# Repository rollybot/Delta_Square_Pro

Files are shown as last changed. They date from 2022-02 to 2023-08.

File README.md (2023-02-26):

# Delta Square Pro
Enclosed chamber-type Delta 3D printer.
You can find the BOM and some parts for this printer at www.rollybot.com website.

제품_Delta Square v1_대표이미지01
The current revision is V1.0.

## Highlights
- Delta (Enclosed chamber-type)
- Minimal design
- 180x180 build volume (bed size : 200mm)
- Enclosed chamber
- Integrated nozzle headset
- 220v / 110v AC
 
## Release History
### V1.0 Initial release (2022 February)
See https://

rollybot.com Logo

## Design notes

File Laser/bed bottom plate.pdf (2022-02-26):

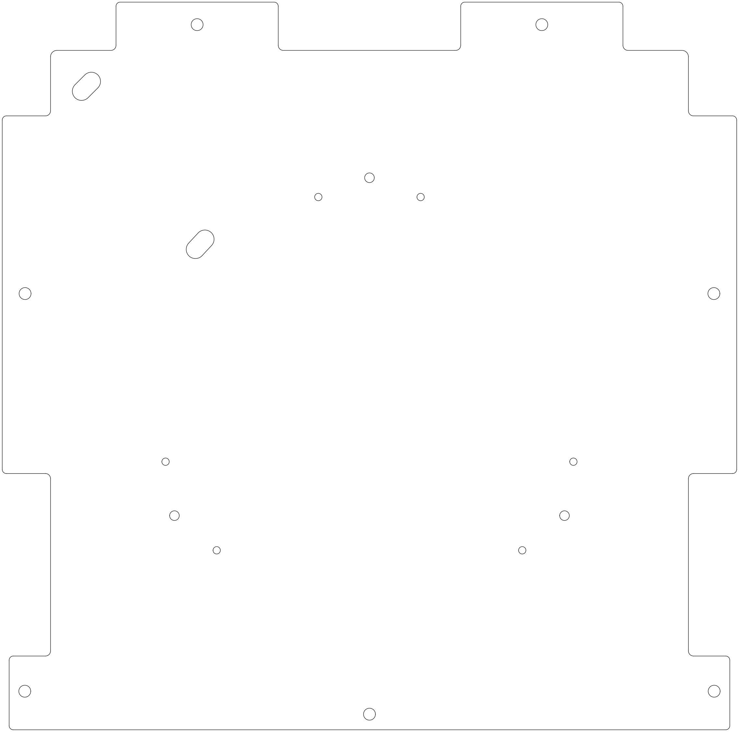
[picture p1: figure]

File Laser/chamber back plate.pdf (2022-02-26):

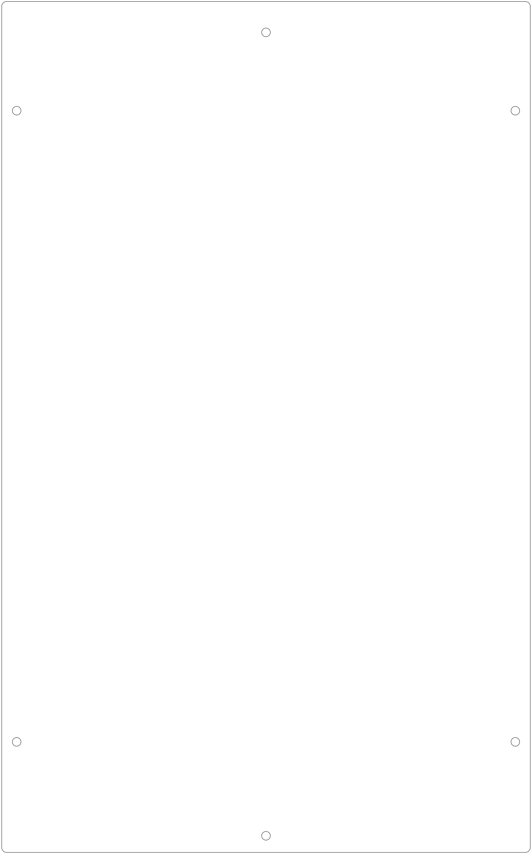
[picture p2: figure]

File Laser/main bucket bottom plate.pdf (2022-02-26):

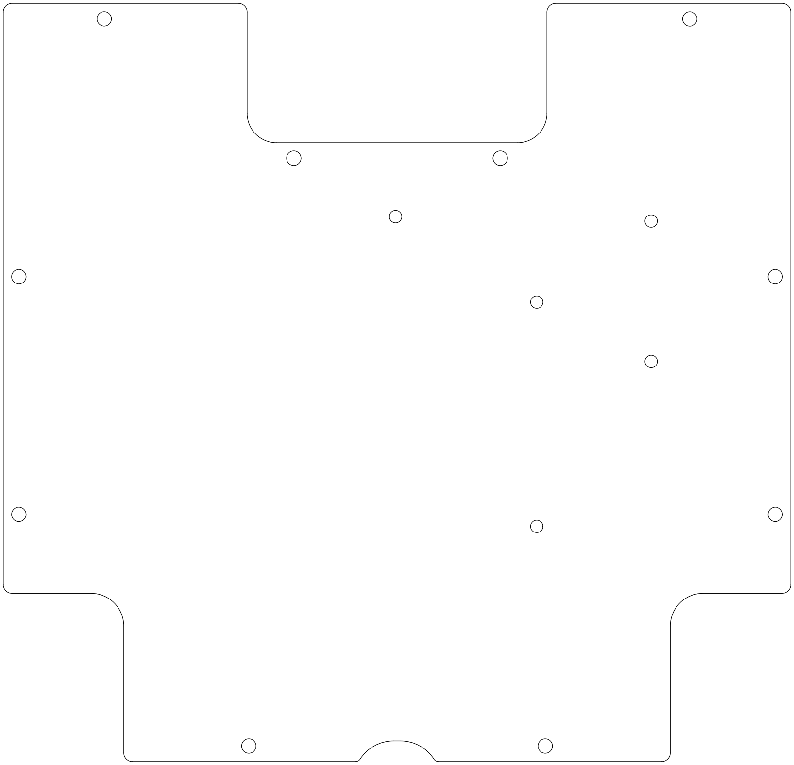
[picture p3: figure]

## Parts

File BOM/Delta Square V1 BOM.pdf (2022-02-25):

Model: Delta Square V1
Developer: rollybot.com
Component | details | Qty | Link
AL profile 2020 280mm | china standard | 6
AL profile 2020 320mm | china standard | 4
AL profile 2020 570mm | china standard | 5
2020 Corner Angle L Bracket | black | 28
20 Series T-nut | M5
GT2 Idler Timing Pulley | 20teeth,6width,5bore,no teeth
Knurled Brass Hot Melt Inset | M3, 5dia, 4.2length
Copper hollow rivet | M4, 4length
POM Bearings Pulley Wheel | 5bore, 21.5dia, 7depth
Right Angle USB Type B male to USB B female extension cable | 30cm
M3 Fisheye Effector Connector | 40mm, Aluminum
Lattice Glass Bed | 200mm, round
Fisheye Ball Bearing Rod Ends Joint | male thread M3
Hollow Carbon Rod | ID3 OD5, 200mm
SAMS socket head cap screw M5 | 10mm, silver
Self-locking nut M5
Hexagon socket button head cap screw M5 | 25mm, silver | 9
Hexagon socket button head cap screw M5 | 20mm, silver | 3
Hexagon socket button head cap screw M5 | 15mm, black
Hexagon socket button head cap screw M5 | 10mm, black
Hexagon socket button head cap screw M5 | 8mm, black
SAMS socket head cap screw M3 | 20mm, silver | 12
Self-locking nut M3
Hexagon socket button head cap screw M3 | 6mm, black

Bill of Materials

Hexagon socket button head cap screw M3 | 8mm, black
Hexagon socket button head cap screw M3 | 10mm, black
Hexagon socket button head cap screw M3 | 12mm, black
Hexagon socket button head cap screw M3 | 15mm, black
Hexagon socket button head cap screw M3 | 22mm, black | 2
Hexagon socket button head cap screw M3 | 35mm, black | 7
NEMA17 | 38mm or 40mm | 4
GT2 Timing Belt | 6mm width
GT2 Timing Pulley | 20teeth,6width,5bore | 3
GT2 Idler Pulley | 20teeth,6width,5bore,no teeth | 3
Print Head PCB | 1.6t | 1 | rollybot.com
Slider PCB | 1.6t | 3 | rollybot.com
Ramps1.4 | | 1
Arduino MEGA 2560 | | 1
2004 LCD | | 1
Timing belt | GT2, 6mm width
Timing belt torsion spring | 6mm width | 3
E3D v6 set (0.4mm nozzle) | | 1
FAN 30x30 | 12v, 10mm width | 2
FAN 50x50 | 12v, 10mm width | 1
CR10 extruder set | right hand type | 1
TMC2208 driver | standalone type | 4
Direct LAN cable | 24awg, 1M | 1
Spacer POM M5 | 12mm, ID5 OD9 | 9
PTFE tube | ID2 OD4
24AWG 2-wire cable
240V power cable
White heat shrink tube | OD 7mm

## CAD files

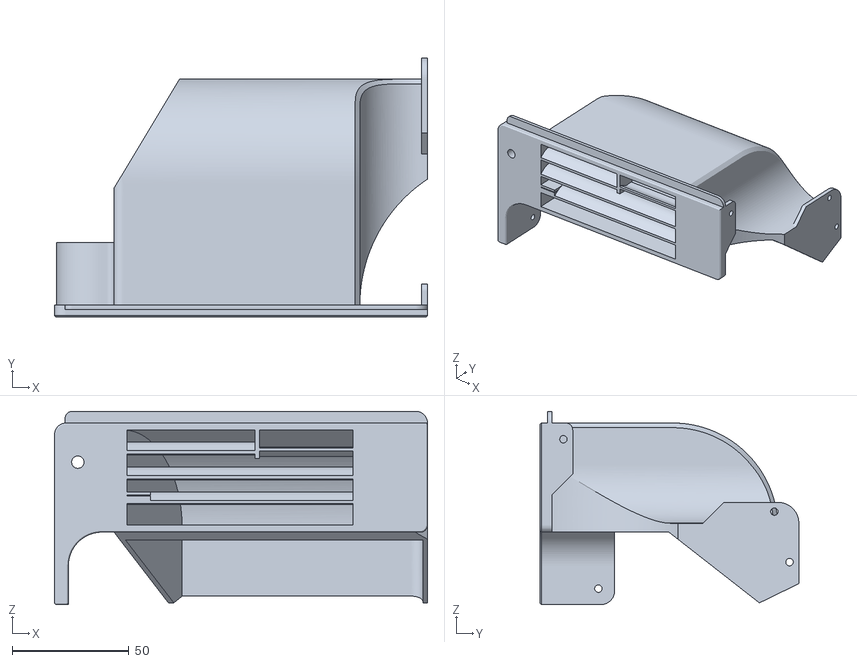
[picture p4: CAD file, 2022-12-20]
STLs/Filter mainvent_right.stl
160.0 x 111.0 x 82.9

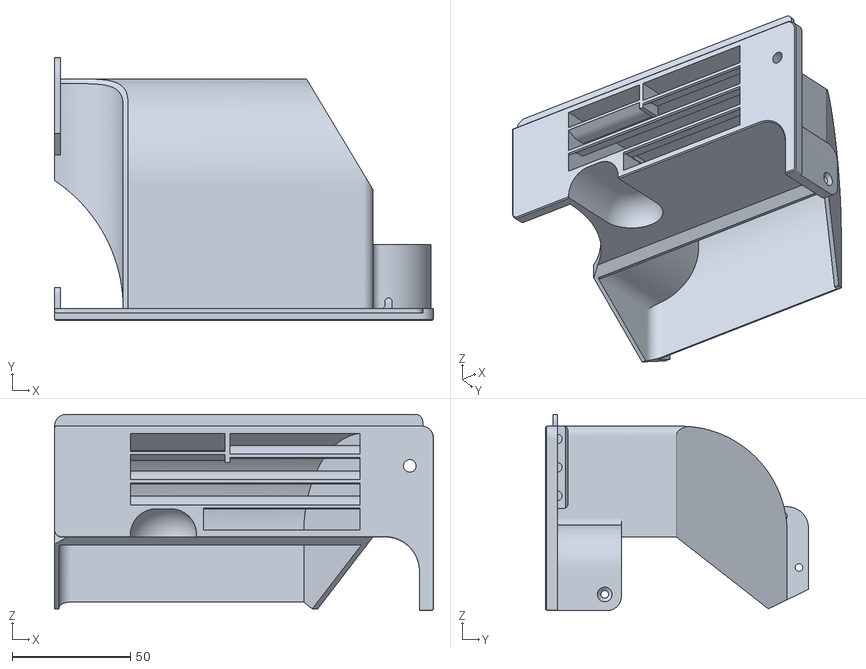
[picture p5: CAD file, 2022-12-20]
STLs/Filter mainvent_left.stl
160.0 x 111.0 x 82.9

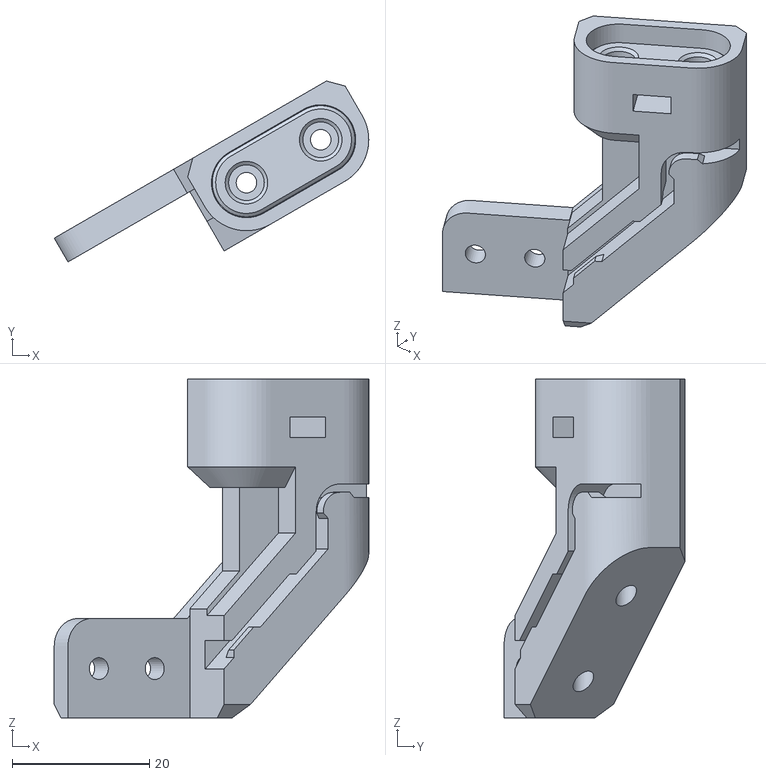
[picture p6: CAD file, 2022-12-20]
STLs/Acc/Fixed leveling sensor.stl
45.8 x 26.4 x 49.4

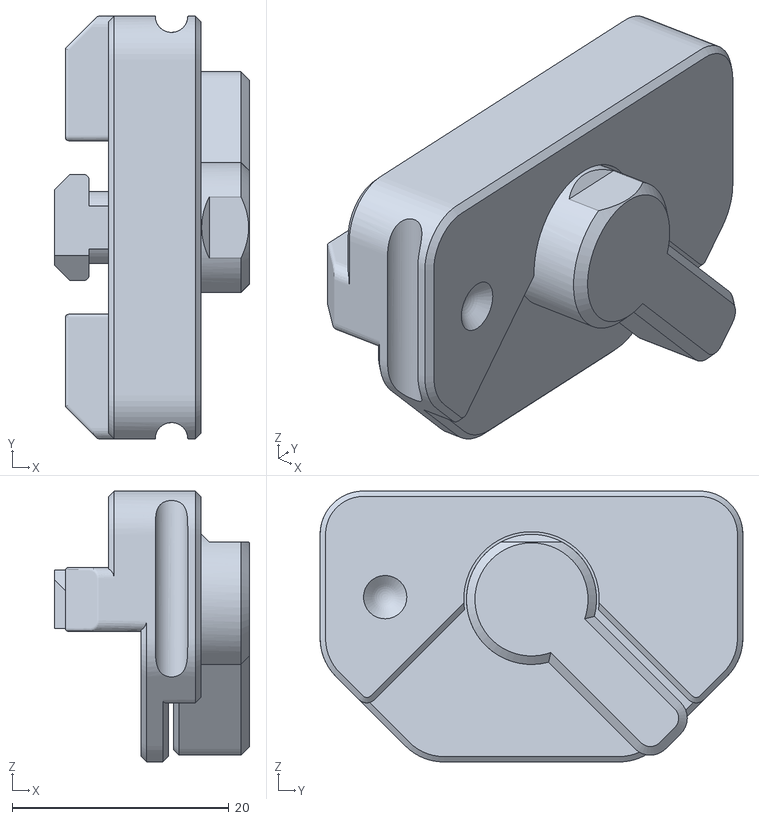
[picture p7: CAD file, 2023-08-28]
STLs/Panel_locker.stl
18.0 x 39.0 x 25.0

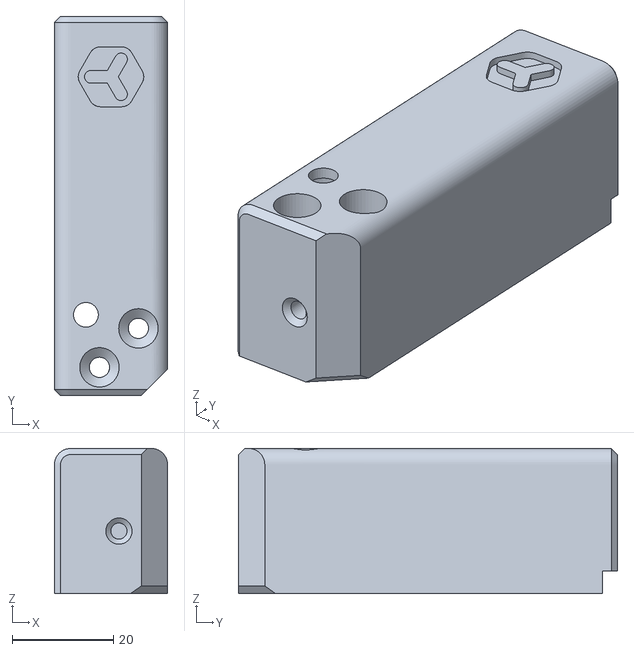
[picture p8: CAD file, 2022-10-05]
STLs/Acc/Filament 45cutter_body.stl
22.4 x 75.0 x 28.7

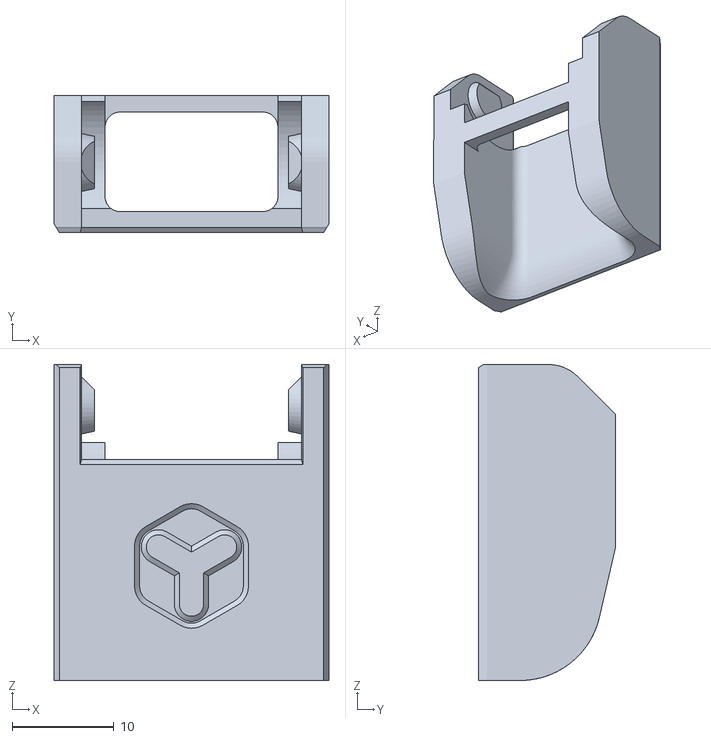
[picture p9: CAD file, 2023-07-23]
STLs/Wire_guide_33.stl
27.0 x 13.5 x 31.1

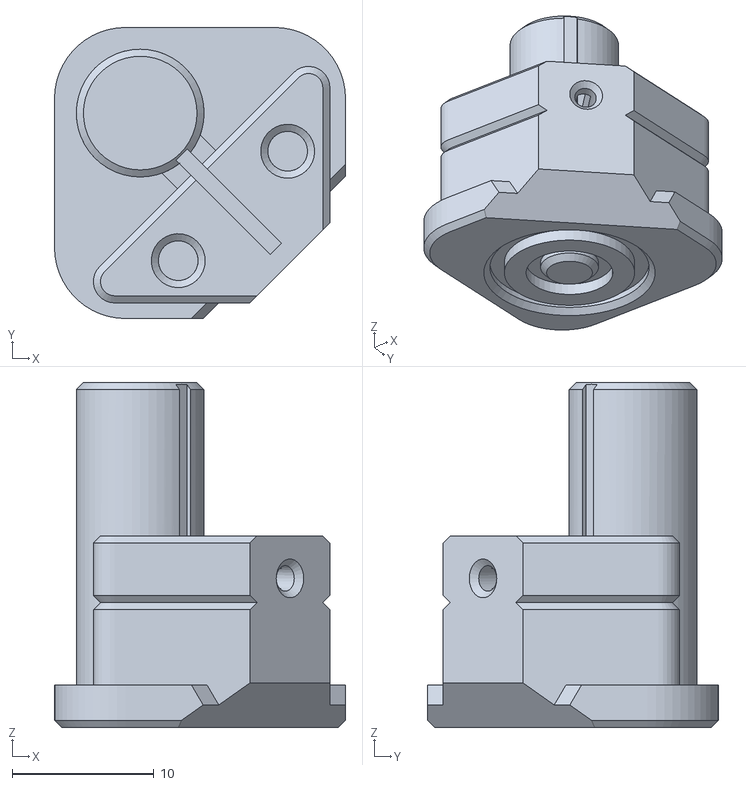
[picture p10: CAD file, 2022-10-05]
STLs/Acc/Filament 45cutter_pusher.stl
20.5 x 20.5 x 24.3

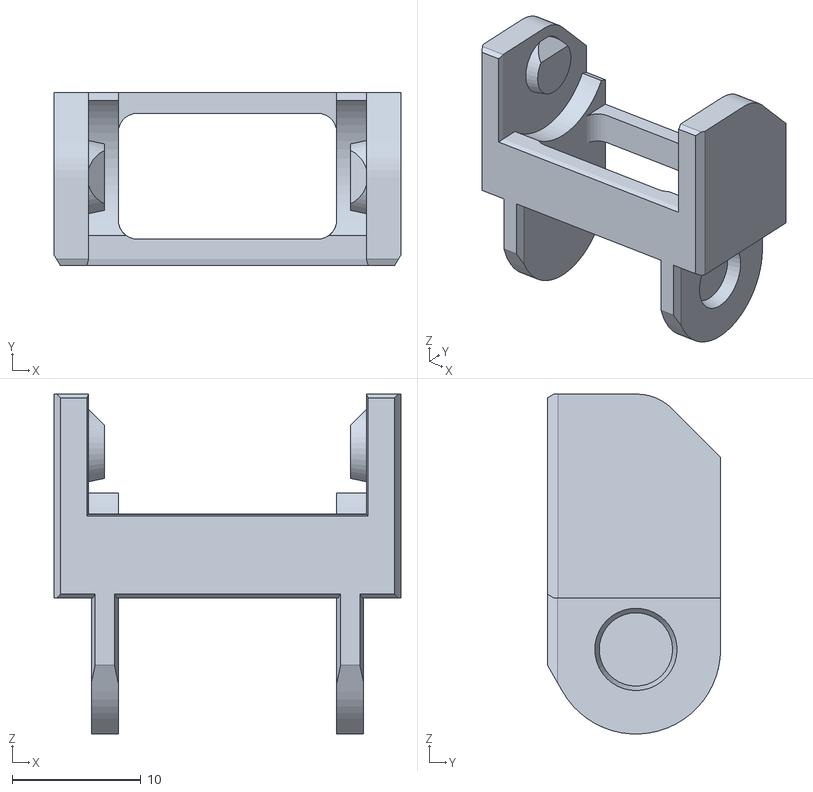
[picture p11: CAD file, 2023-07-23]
STLs/Wire_guide_23.stl
27.0 x 13.5 x 26.5

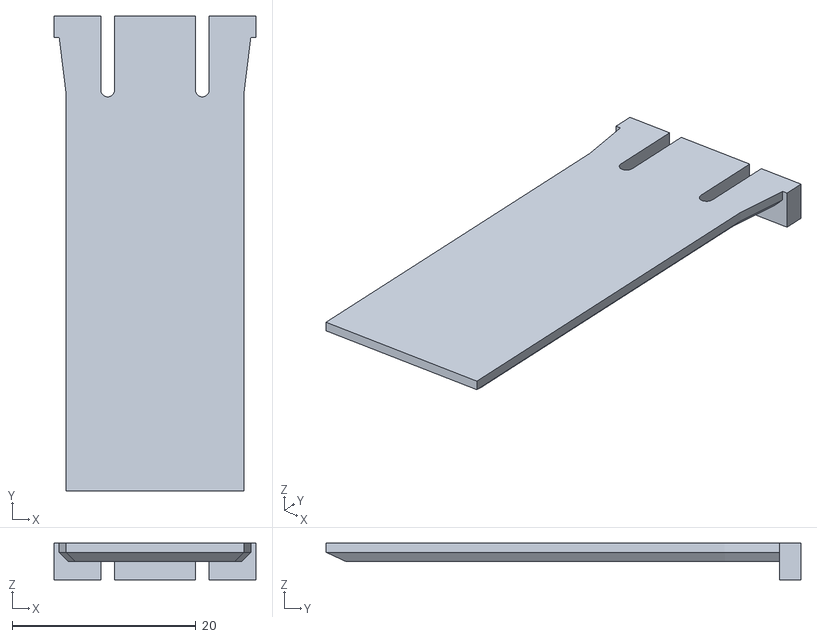
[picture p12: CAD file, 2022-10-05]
STLs/Acc/Filament 45cutter_cover.stl
22.0 x 51.7 x 4.00

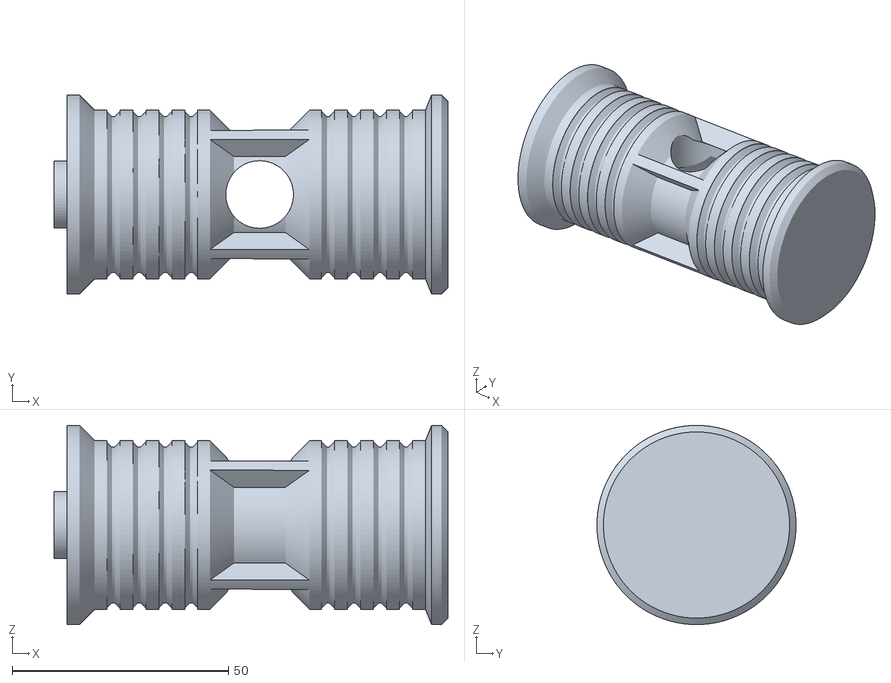
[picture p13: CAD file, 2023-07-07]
STLs/spool core.stl
91.0 x 46.0 x 46.0

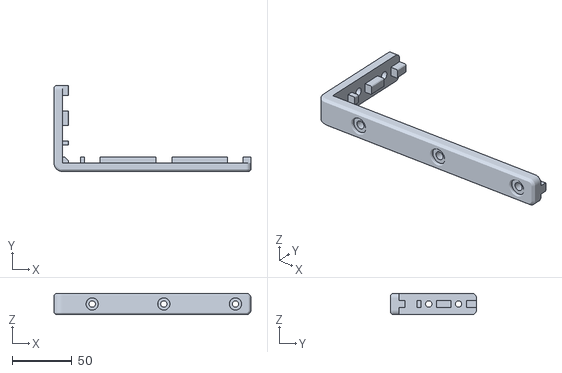
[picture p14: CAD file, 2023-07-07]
STLs/Frame longLbar.stl
165.0 x 72.0 x 18.0

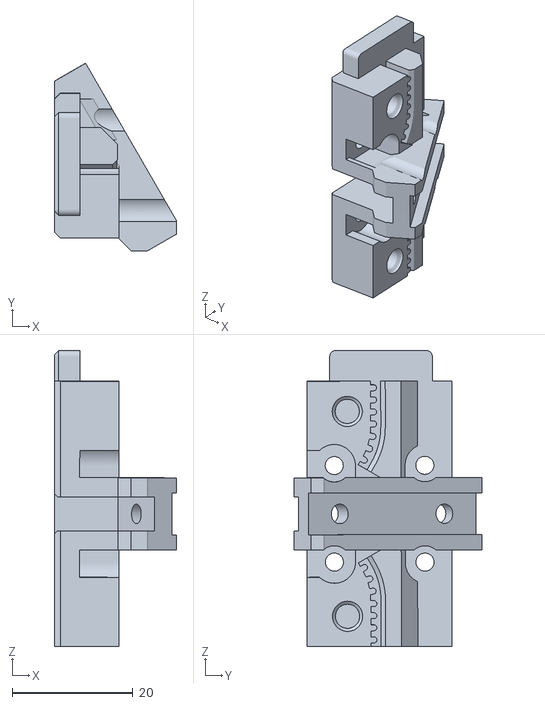
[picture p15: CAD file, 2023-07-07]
STLs/X-slider.stl
20.2 x 31.1 x 49.0

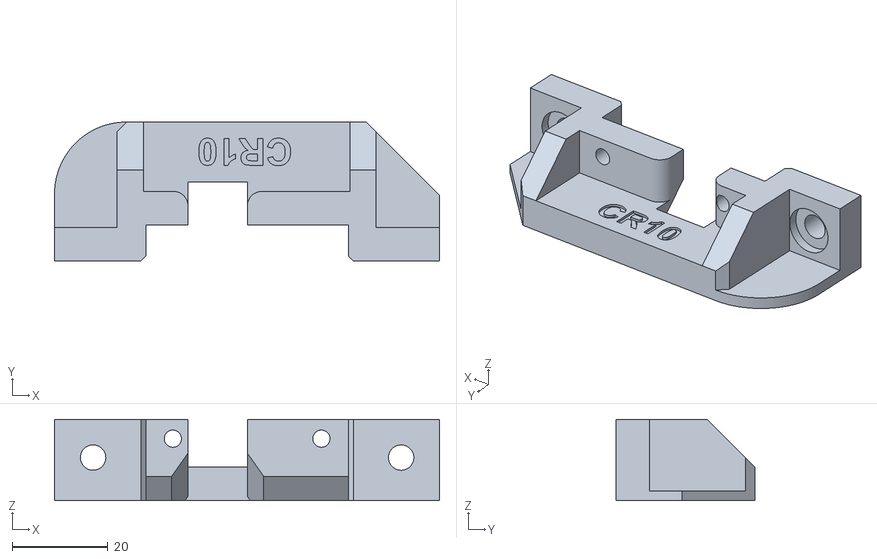
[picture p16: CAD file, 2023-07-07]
STLs/E-motor bracket_CR10.stl
80.4 x 29.0 x 17.0

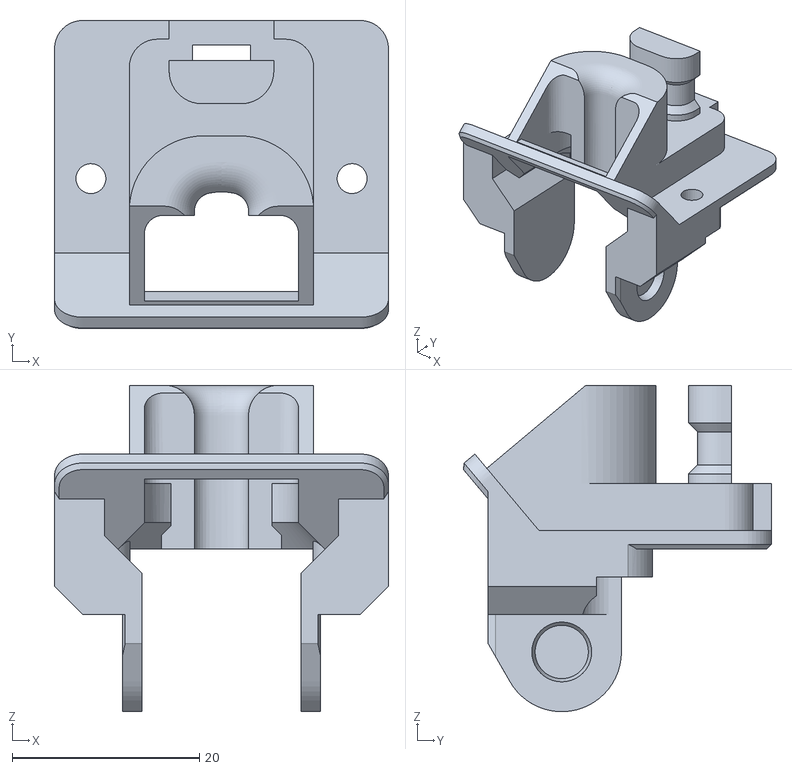
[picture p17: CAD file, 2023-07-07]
STLs/Top bucket front_hole.stl
35.7 x 32.9 x 34.9

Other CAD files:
STLs/Top bucket side left.stl
STLs/XY-slider cover.stl
STLs/Z-slider.stl
STLs/Door hinge rota.stl
STLs/Delta arm shoe.stl
STLs/Door hinge stat.stl
STLs/E-motor bracket_MK9.stl
STLs/Filter Lower Bracket_left.stl
STLs/Filter Lower Bracket_right.stl
STLs/Frame DoorGuide-left.stl
STLs/Frame DoorGuide-right.stl
STLs/Frame FootBase.stl
STLs/Frame L bracket-left.stl
STLs/Frame L bracket-right.stl
STLs/HW_MKS_robin_E3D_bracket.stl
STLs/HW_fan guide.stl
STLs/HW_mega2560_bracket.stl
STLs/HW_power_leg_bracket.stl
STLs/LCD Leg left.stl
STLs/LCD Leg right.stl
STLs/LCD front panel.stl
STLs/Top bucket front.stl
STLs/Top bucket rear left.stl
STLs/Top bucket rear right.stl
STLs/Top bucket side right.stl
STLs/Top door guide left.stl
STLs/Top door guide right.stl
STLs/Window_3t Panel Corner.stl
STLs/Window_3t Panel Locker.stl
STLs/X-idle belt supporter.stl
STLs/X-motor bracket.stl
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

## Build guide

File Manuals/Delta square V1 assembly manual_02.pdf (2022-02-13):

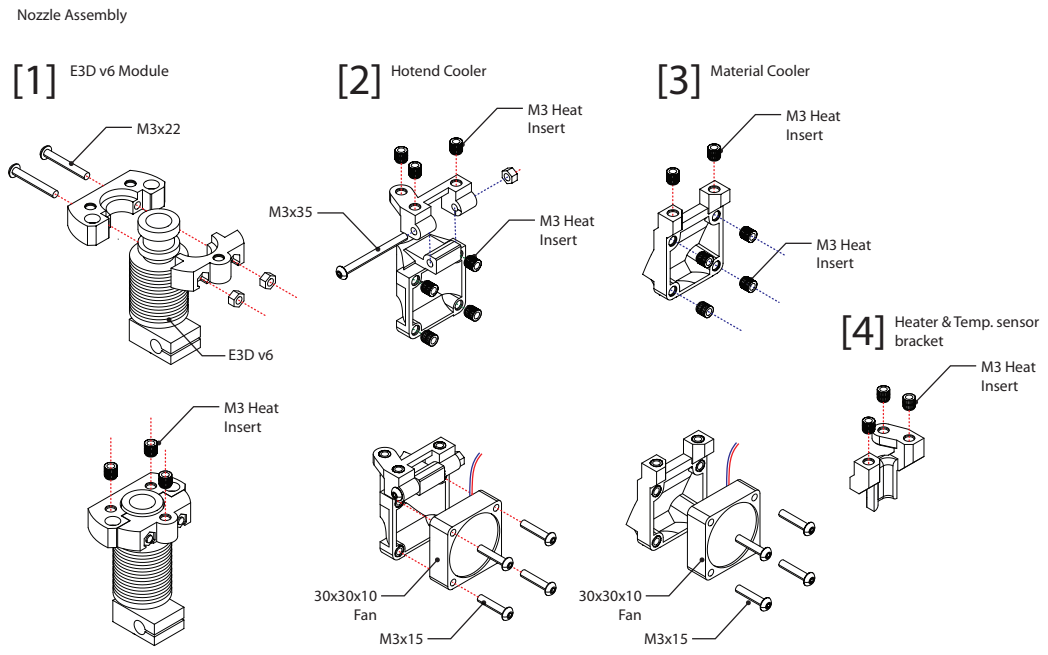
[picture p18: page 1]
Nozzle Assembly; E3D v6 Module; Hotend Cooler [1]; Material Cooler [3]; 30x30x10 Fan; M3 Heat Insert

Heater & Temp. sensor [4] bracket

[5]

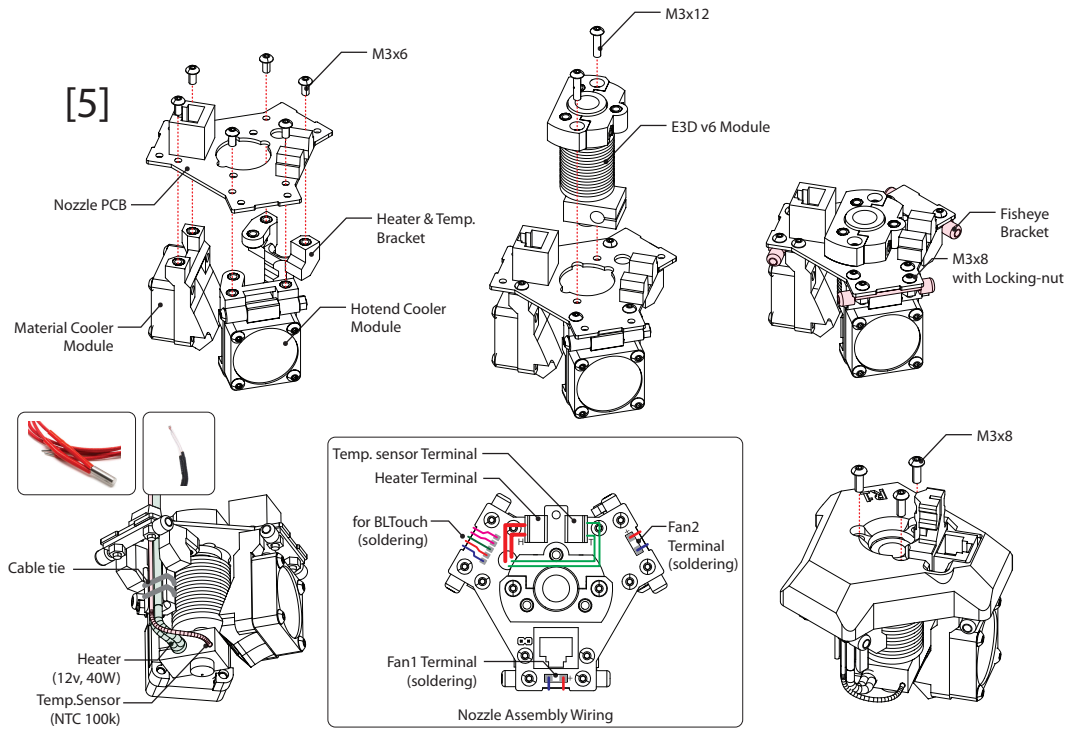
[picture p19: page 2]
E3D v6 Module; for BLTouch (soldering); Fan2 Terminal (soldering); Heater & Temp. Bracket; Hotend Cooler Module; Fisheye Bracket; Nozzle PCB; Material Cooler Module; Heater (12v, 40W); Cable tie; Temp.Sensor (NTC 100k); M3x8 with Locking-nut

Temp. sensor Terminal
Heater Terminal

Fan1 Terminal
(soldering)
Nozzle Assembly Wiring

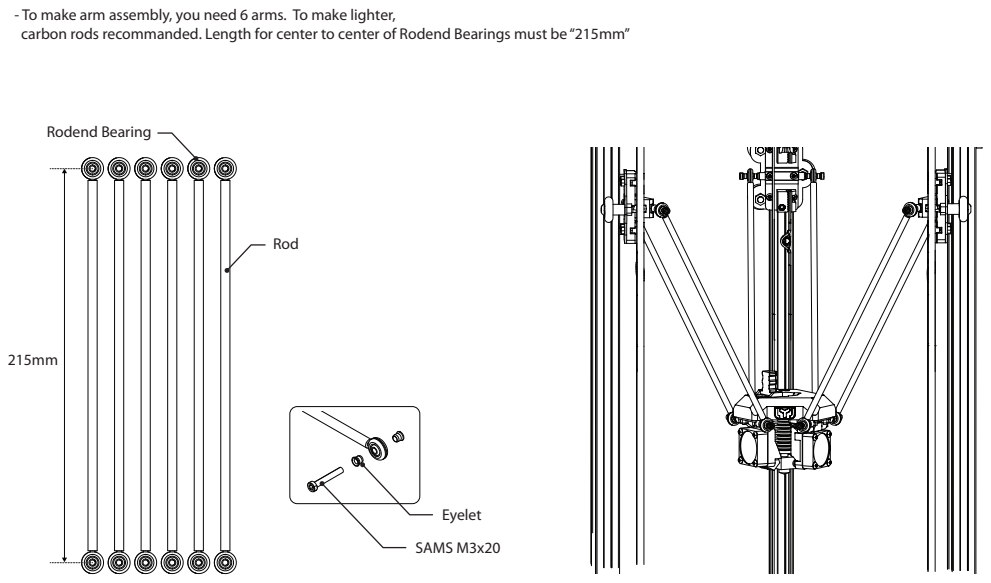
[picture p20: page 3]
Rod; Rodend Bearing; Eyelet; SAMS M3x20

- To make arm assembly, you need 6 arms. To make lighter,
carbon rods recommanded. Length for center to center of Rodend Bearings must be “215mm”

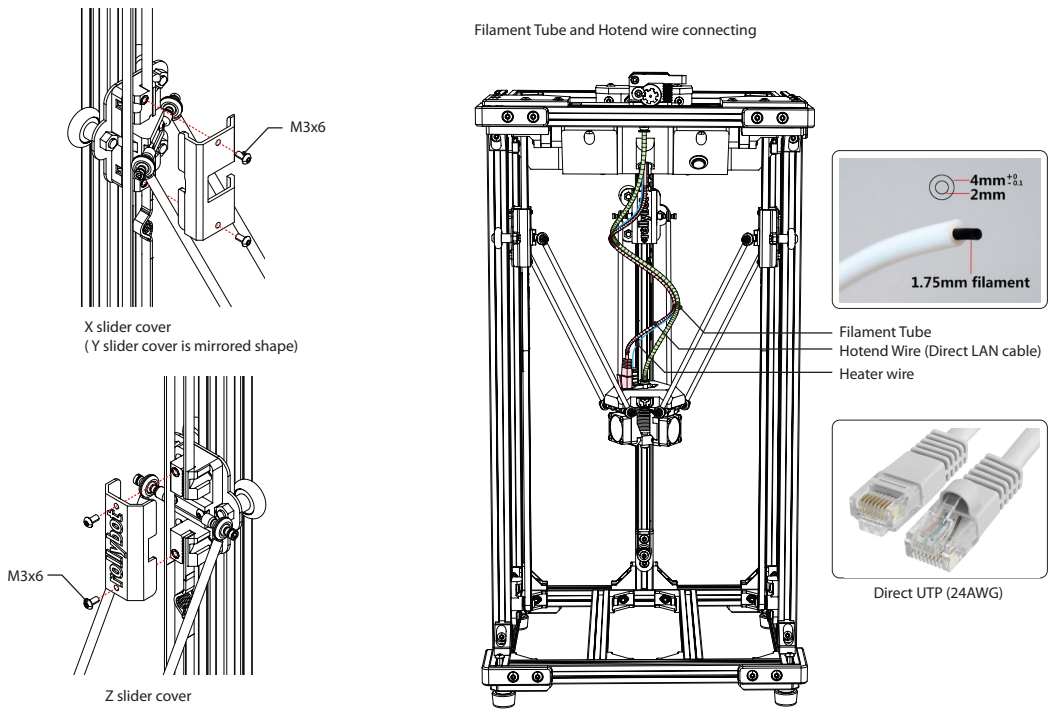
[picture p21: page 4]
Direct UTP (24AWG); Z slider cover

Filament Tube and Hotend wire connecting

X slider cover
( Y slider cover is mirrored shape)

Filament Tube
Hotend Wire (Direct LAN cable)
Heater wire

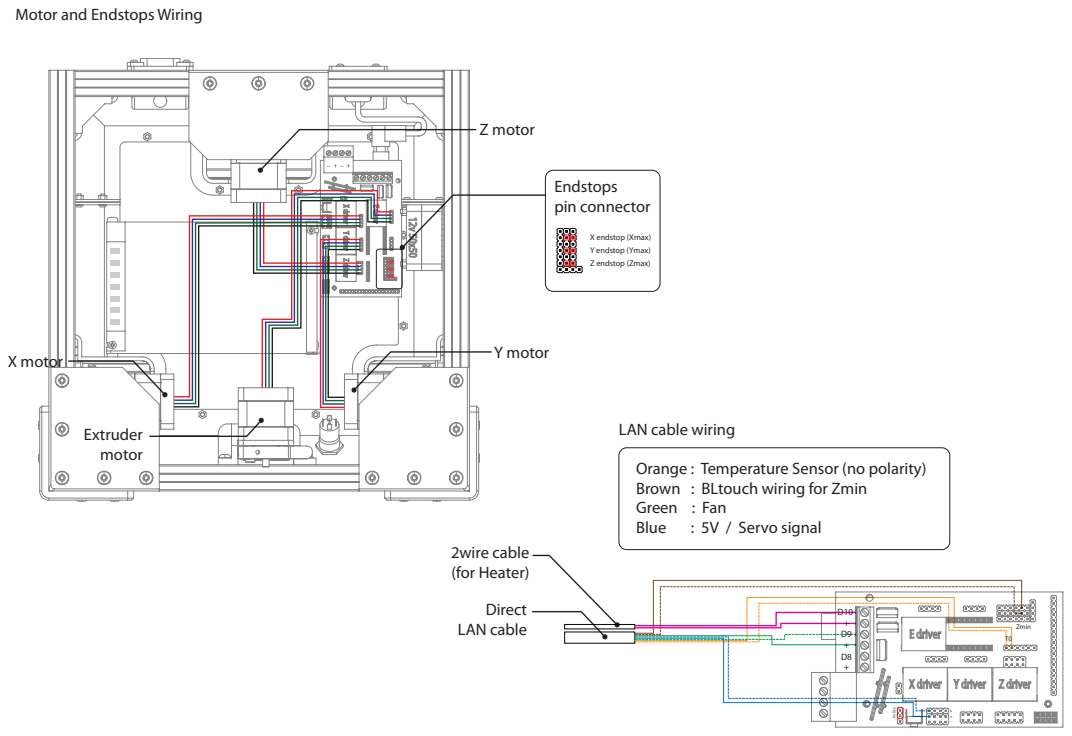
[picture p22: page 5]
Endstops pin connector; Z motor; Y motor; Blue; : 5V / Servo signal; Extruder motor; X motor; Direct LAN cable; 2wire cable (for Heater); X endstop (Xmax) Y endstop (Ymax) Z endstop (Zmax); Zmin; Vcc

Motor and Endstops Wiring

LAN cable wiring

Orange : Temperature Sensor (no polarity)
Brown : BLtouch wiring for Zmin
Green : Fan

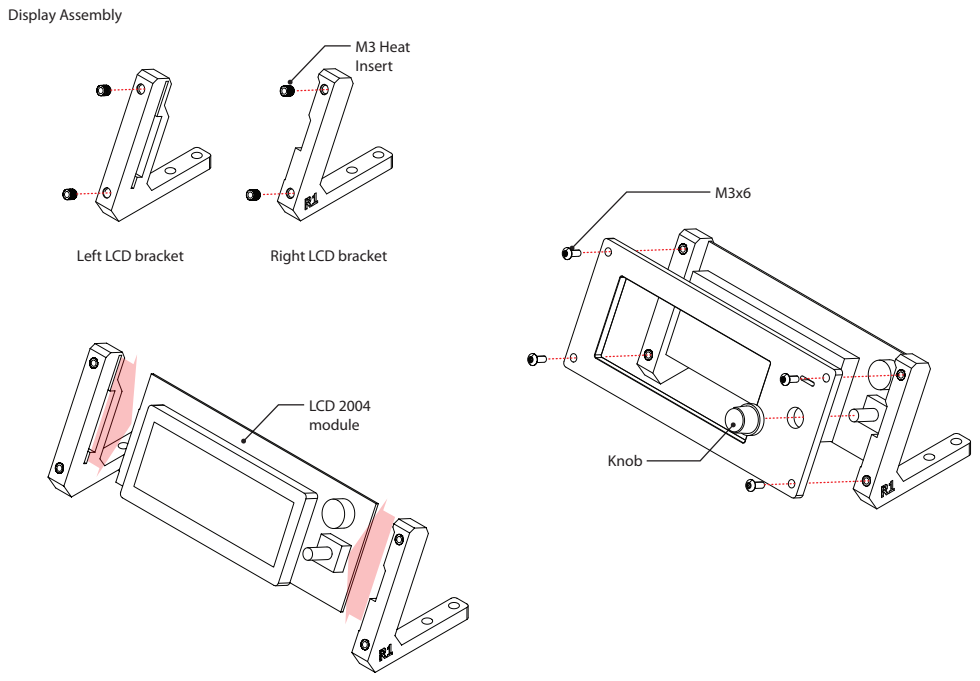
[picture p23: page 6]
Display Assembly; Left LCD bracket; Right LCD bracket; Knob; M3 Heat Insert; LCD 2004 module

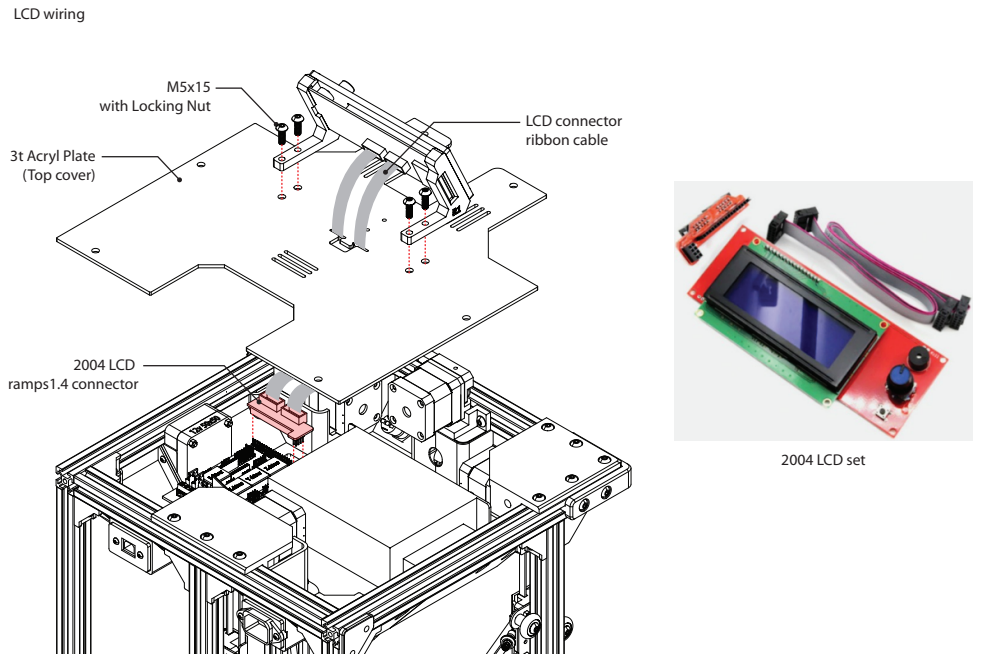
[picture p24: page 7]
LCD wiring; 3t Acryl Plate (Top cover); 2004 LCD ramps1.4 connector; 2004 LCD set; LCD connector ribbon cable

with Locking Nut

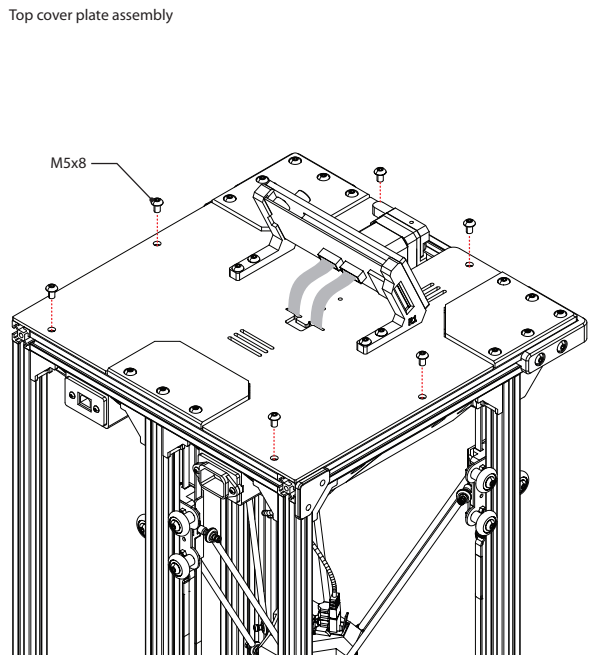
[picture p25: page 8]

Top cover plate assembly

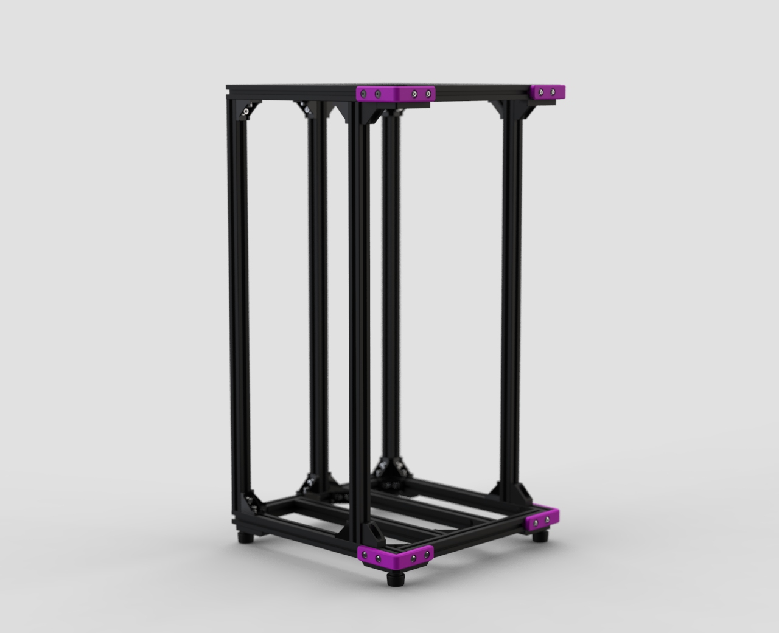
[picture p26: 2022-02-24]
Manuals/Frame Set.jpg

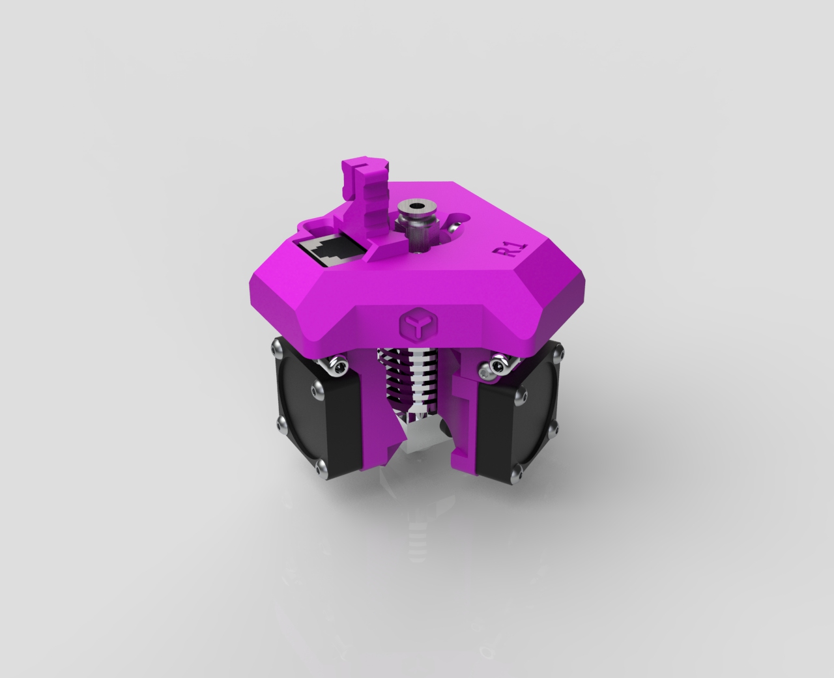
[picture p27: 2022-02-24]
Manuals/Print Head set.jpg

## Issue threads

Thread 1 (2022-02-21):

BOM & CAD

claytono, 2022-02-21:
This looks like a really interesting project.  I don't read Korean, but I looked at the rollybot.com website and don't see the BOM there.  Are you planning to release the CAD for this project?

lyangj, 2022-02-22:
Yes.  I am preparing the bom and files.  Im still uploading other files to github.  I have plan to finish uploading v1 in a month.  And v0 in 3 months.

나의 iPhone에서 보냄

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

Closed 2023-08-28.

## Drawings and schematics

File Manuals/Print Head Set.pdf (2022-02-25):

# Delta Square Print Head Set

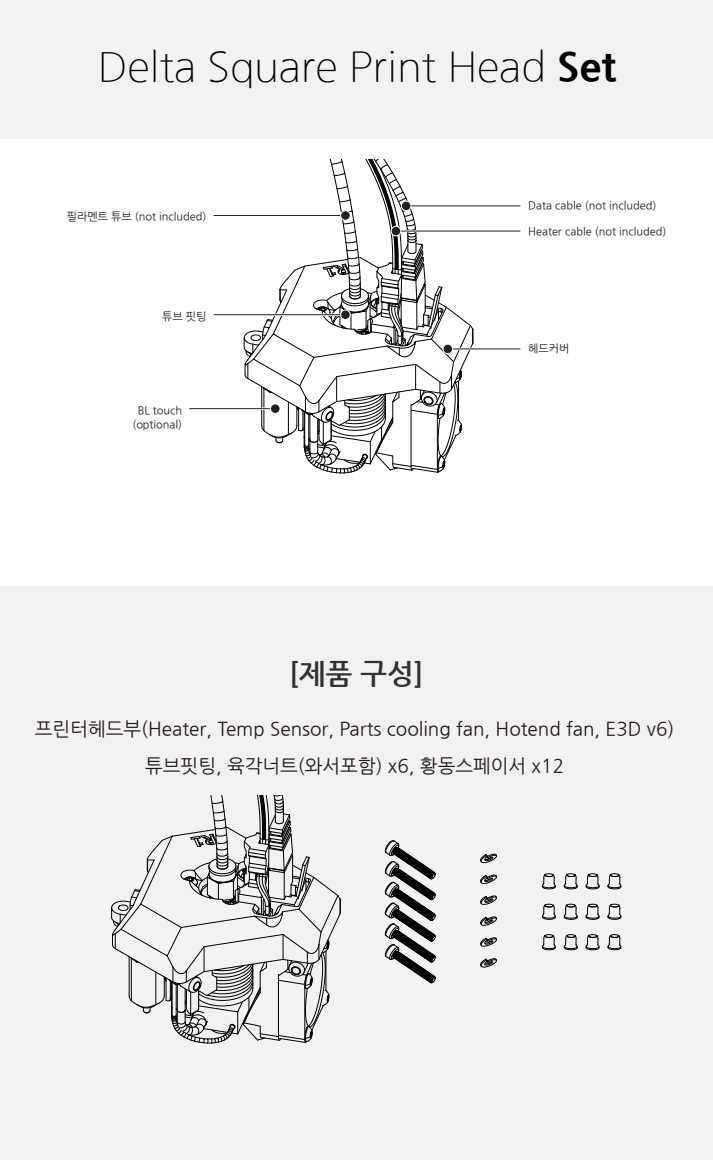
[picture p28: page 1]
헤드커버; BL touch (optional)

Data cable (not included)

필라멘트 튜브 (not included)

Heater cable (not included)

프린터헤드부(Heater, Temp Sensor, Parts cooling fan, Hotend fan, E3D v6)

튜브핏팅, 육각너트(와서포함) x6, 황동스페이서 x12

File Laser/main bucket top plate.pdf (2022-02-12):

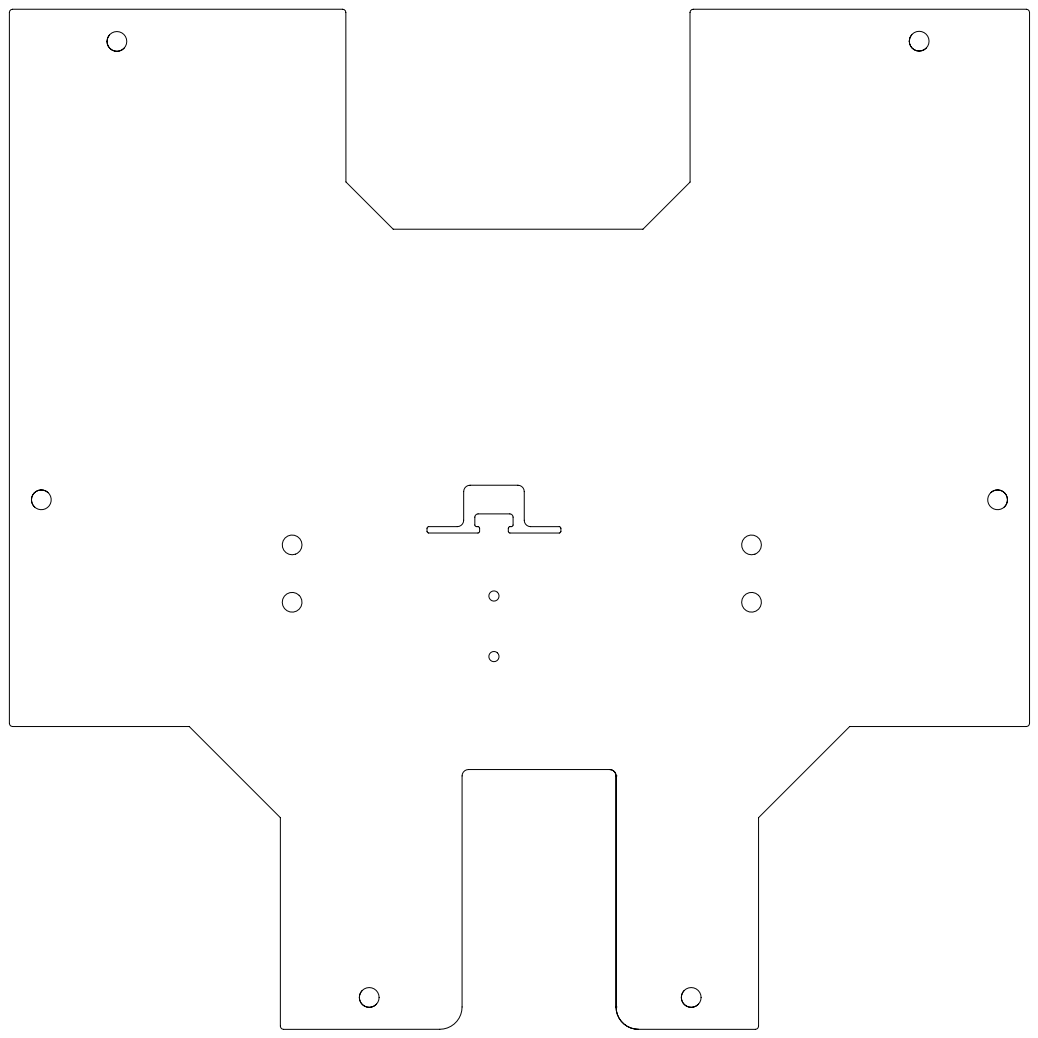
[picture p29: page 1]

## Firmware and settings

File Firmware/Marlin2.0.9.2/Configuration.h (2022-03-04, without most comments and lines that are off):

#pragma once
#define CONFIG_EXAMPLES_DIR "delta/generic"
#define CONFIGURATION_H_VERSION 02000902
#define STRING_CONFIG_H_AUTHOR "rollybot.com" // Who made the changes.
#define SHOW_BOOTSCREEN
#define SERIAL_PORT 0
#define BAUDRATE 250000
  #define MOTHERBOARD BOARD_RAMPS_14_EFB
#define CUSTOM_MACHINE_NAME "Delta Square v1.4"
#if LINEAR_AXES >= 4
  #define AXIS4_NAME 'A' // :['A', 'B', 'C', 'U', 'V', 'W']
#endif
#if LINEAR_AXES >= 5
  #define AXIS5_NAME 'B' // :['A', 'B', 'C', 'U', 'V', 'W']
#endif
#if LINEAR_AXES >= 6
  #define AXIS6_NAME 'C' // :['A', 'B', 'C', 'U', 'V', 'W']
#endif
#define EXTRUDERS 1
#define DEFAULT_NOMINAL_FILAMENT_DIA 1.75
#define PSU_CONTROL
  #define PSU_ACTIVE_STATE LOW      // Set 'LOW' for ATX, 'HIGH' for X-Box
#define TEMP_SENSOR_0 1
#define TEMP_SENSOR_1 0
#define TEMP_SENSOR_2 0
#define TEMP_SENSOR_3 0
#define TEMP_SENSOR_4 0
#define TEMP_SENSOR_5 0
#define TEMP_SENSOR_6 0
#define TEMP_SENSOR_7 0
#define TEMP_SENSOR_BED 0     // 11, for keenovo AC hotbed (rollybot)
#define TEMP_SENSOR_PROBE 0
#define TEMP_SENSOR_CHAMBER 0
#define TEMP_SENSOR_COOLER 0
#define TEMP_SENSOR_BOARD 0
#define TEMP_SENSOR_REDUNDANT 0
#define DUMMY_THERMISTOR_998_VALUE  25
#define DUMMY_THERMISTOR_999_VALUE 100
#define TEMP_RESIDENCY_TIME         10  // (seconds) Time to wait for hotend to "settle" in M109
#define TEMP_WINDOW                  1  // (°C) Temperature proximity for the "temperature reached" timer
#define TEMP_HYSTERESIS              3  // (°C) Temperature proximity considered "close enough" to the target
#define TEMP_BED_RESIDENCY_TIME      0  // (seconds) Time to wait for bed to "settle" in M190
#define TEMP_BED_WINDOW              1  // (°C) Temperature proximity for the "temperature reached" timer
#define TEMP_BED_HYSTERESIS          3  // (°C) Temperature proximity considered "close enough" to the target
#define TEMP_CHAMBER_RESIDENCY_TIME 10  // (seconds) Time to wait for chamber to "settle" in M191
#define TEMP_CHAMBER_WINDOW          1  // (°C) Temperature proximity for the "temperature reached" timer
#define TEMP_CHAMBER_HYSTERESIS      3  // (°C) Temperature proximity considered "close enough" to the target
#if TEMP_SENSOR_REDUNDANT
  #define TEMP_SENSOR_REDUNDANT_SOURCE    E1  // The sensor that will provide the redundant reading.
  #define TEMP_SENSOR_REDUNDANT_TARGET    E0  // The sensor that we are providing a redundant reading for.
  #define TEMP_SENSOR_REDUNDANT_MAX_DIFF  10  // (°C) Temperature difference that will trigger a print abort.
#endif
#define HEATER_0_MINTEMP   5
#define HEATER_1_MINTEMP   5
#define HEATER_2_MINTEMP   5
#define HEATER_3_MINTEMP   5
#define HEATER_4_MINTEMP   5
#define HEATER_5_MINTEMP   5
#define HEATER_6_MINTEMP   5
#define HEATER_7_MINTEMP   5
#define BED_MINTEMP        5
#define CHAMBER_MINTEMP    5
#define HEATER_0_MAXTEMP 275
#define HEATER_1_MAXTEMP 275
#define HEATER_2_MAXTEMP 275
#define HEATER_3_MAXTEMP 275
#define HEATER_4_MAXTEMP 275
#define HEATER_5_MAXTEMP 275
#define HEATER_6_MAXTEMP 275
#define HEATER_7_MAXTEMP 275
#define BED_MAXTEMP      150
#define CHAMBER_MAXTEMP  60
#define HOTEND_OVERSHOOT 15   // (°C) Forbid temperatures over MAXTEMP - OVERSHOOT
#define BED_OVERSHOOT    10   // (°C) Forbid temperatures over MAXTEMP - OVERSHOOT
#define COOLER_OVERSHOOT  2   // (°C) Forbid temperatures closer than OVERSHOOT
#define PIDTEMP
#define BANG_MAX 255     // Limits current to nozzle while in bang-bang mode; 255=full current
#define PID_MAX BANG_MAX // Limits current to nozzle while PID is active (see PID_FUNCTIONAL_RANGE below); 255=full current
#define PID_K1 0.95      // Smoothing factor within any PID loop
    #define DEFAULT_Kp  22.20
    #define DEFAULT_Ki   1.08
    #define DEFAULT_Kd 114.00
#define MAX_BED_POWER 255 // limits duty cycle to bed; 255=full current
#define MAX_CHAMBER_POWER 255 // limits duty cycle to chamber heater; 255=full current
  #define PID_FUNCTIONAL_RANGE 10 // If the temperature difference between the target temperature and the actual temperature
#define PREVENT_COLD_EXTRUSION
#define EXTRUDE_MINTEMP 200            // rollybot, before 170
#define PREVENT_LENGTHY_EXTRUDE
#define EXTRUDE_MAXLENGTH 600           // rollybot, before 200
#define THERMAL_PROTECTION_HOTENDS // Enable thermal protection for all extruders
#define THERMAL_PROTECTION_BED     // Enable thermal protection for the heated bed
#define THERMAL_PROTECTION_CHAMBER // Enable thermal protection for the heated chamber
#define THERMAL_PROTECTION_COOLER  // Enable thermal protection for the laser cooling
#define DELTA
  #define DELTA_SEGMENTS_PER_SECOND 200
  #define DELTA_PRINTABLE_RADIUS 91.0    // (mm)   180mm dia
  #define DELTA_MAX_RADIUS       95.0    // (mm)
  #define DELTA_DIAGONAL_ROD 215.0       // (mm)
  #define DELTA_HEIGHT 237.00            // (mm)  VO series :         V1 series : 257.00
  #define DELTA_ENDSTOP_ADJ { 0.0, 0.0, 0.0 } // Get these values from G33 auto calibrate
  #define DELTA_RADIUS 102.5900               // (mm) Get this value from G33 auto calibrate
  #define DELTA_TOWER_ANGLE_TRIM { 0.0, 0.0, 0.0 } // Get these values from G33 auto calibrate
#define USE_ZMIN_PLUG // a Z probe
#define USE_XMAX_PLUG
#define USE_YMAX_PLUG
#define USE_ZMAX_PLUG
#define ENDSTOPPULLUPS
#define X_MIN_ENDSTOP_INVERTING false  // Set to true to invert the logic of the endstop.
#define Y_MIN_ENDSTOP_INVERTING false  // Set to true to invert the logic of the endstop.
#define Z_MIN_ENDSTOP_INVERTING false  // Set to true to invert the logic of the endstop.
#define I_MIN_ENDSTOP_INVERTING false  // Set to true to invert the logic of the endstop.
#define J_MIN_ENDSTOP_INVERTING false  // Set to true to invert the logic of the endstop.
#define K_MIN_ENDSTOP_INVERTING false  // Set to true to invert the logic of the endstop.
#define X_MAX_ENDSTOP_INVERTING false  // Set to true to invert the logic of the endstop.
#define Y_MAX_ENDSTOP_INVERTING false  // Set to true to invert the logic of the endstop.
#define Z_MAX_ENDSTOP_INVERTING false  // Set to true to invert the logic of the endstop.
#define I_MAX_ENDSTOP_INVERTING false  // Set to true to invert the logic of the endstop.
#define J_MAX_ENDSTOP_INVERTING false  // Set to true to invert the logic of the endstop.
#define K_MAX_ENDSTOP_INVERTING false  // Set to true to invert the logic of the endstop.
#define Z_MIN_PROBE_ENDSTOP_INVERTING false  // Set to true to invert the logic of the probe.
#define X_DRIVER_TYPE  TMC2208_STANDALONE   // Vref = 1.0A for NEMA17 40mm
#define Y_DRIVER_TYPE  TMC2208_STANDALONE
#define Z_DRIVER_TYPE  TMC2208_STANDALONE
#define E0_DRIVER_TYPE TMC2208_STANDALONE   // Vref = 1.0A for NEMA17 40mm , 0.5A for Orbiter
#define XYZ_FULL_STEPS_PER_ROTATION 200
#define XYZ_MICROSTEPS 16
#define XYZ_BELT_PITCH 2
#define XYZ_PULLEY_TEETH 20
#define DEFAULT_XYZ_STEPS_PER_UNIT ((XYZ_FULL_STEPS_PER_ROTATION) * (XYZ_MICROSTEPS) / double(XYZ_BELT_PITCH) / double(XYZ_PULLEY_TEETH))
#define DEFAULT_AXIS_STEPS_PER_UNIT   { DEFAULT_XYZ_STEPS_PER_UNIT, DEFAULT_XYZ_STEPS_PER_UNIT, DEFAULT_XYZ_STEPS_PER_UNIT, 92.60 }   // 3200 / (extrude gear dia(11.0) * 3.14) = 92.65
#define DEFAULT_MAX_FEEDRATE          { 500, 500, 500, 25 }
#define DEFAULT_MAX_ACCELERATION      { 9000, 9000, 9000, 10000 }  // for direct extruder , 7000 cause of heavier
#define DEFAULT_ACCELERATION          2000    // X, Y, Z and E acceleration for printing moves
#define DEFAULT_RETRACT_ACCELERATION  2000    // E acceleration for retracts
#define DEFAULT_TRAVEL_ACCELERATION   1000    // X, Y, Z acceleration for travel (non printing) moves
#define CLASSIC_JERK
  #define DEFAULT_XJERK 5.0
  #define DEFAULT_YJERK DEFAULT_XJERK
  #define DEFAULT_ZJERK DEFAULT_XJERK // Must be same as XY for delta
#define DEFAULT_EJERK    5.0  // May be used by Linear Advance
#define Z_MIN_PROBE_USES_Z_MIN_ENDSTOP_PIN
#define PROBE_MANUALLY
#define NOZZLE_TO_PROBE_OFFSET { 22.5, 13.0, -1.20 }    // rollybot
#define PROBING_MARGIN 10
#define XY_PROBE_FEEDRATE (66*60)
#define Z_PROBE_FEEDRATE_FAST (100*60)   // before 200
#define Z_PROBE_FEEDRATE_SLOW (Z_PROBE_FEEDRATE_FAST / 2)
#define Z_CLEARANCE_DEPLOY_PROBE   15 // Z Clearance for Deploy/Stow
#define Z_CLEARANCE_BETWEEN_PROBES  5 // Z Clearance between probe points
#define Z_CLEARANCE_MULTI_PROBE     5 // Z Clearance between multiple probes
#define Z_PROBE_LOW_POINT          -2 // Farthest distance below the trigger-point to go before stopping
#define Z_PROBE_OFFSET_RANGE_MIN -20
#define Z_PROBE_OFFSET_RANGE_MAX 20
#define X_ENABLE_ON 0
#define Y_ENABLE_ON 0
#define Z_ENABLE_ON 0
#define E_ENABLE_ON 0 // For all extruders
#define DISABLE_X false
#define DISABLE_Y false
#define DISABLE_Z false
#define DISABLE_E false             // Disable the extruder when not stepping
#define DISABLE_INACTIVE_EXTRUDER   // Keep only the active extruder enabled
#define INVERT_X_DIR false
#define INVERT_Y_DIR true
#define INVERT_Z_DIR false
#define INVERT_E0_DIR true
#define INVERT_E1_DIR false
#define INVERT_E2_DIR false
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

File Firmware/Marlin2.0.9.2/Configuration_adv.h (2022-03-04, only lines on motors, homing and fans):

#define FAN_PIN -1           //  has to add this code
#define E0_AUTO_FAN_PIN  9   // D9 , (rollybot)
#define E1_AUTO_FAN_PIN -1
#define E2_AUTO_FAN_PIN -1
#define E3_AUTO_FAN_PIN -1
#define E4_AUTO_FAN_PIN -1
#define E5_AUTO_FAN_PIN -1
#define E6_AUTO_FAN_PIN -1
#define E7_AUTO_FAN_PIN -1
#define CHAMBER_AUTO_FAN_PIN -1
#define COOLER_AUTO_FAN_PIN -1
#define COOLER_FAN_PIN -1
#define HOMING_BUMP_MM      { 5, 5, 5 }       // (mm) Backoff from endstops after first bump
#define HOMING_BUMP_DIVISOR { 5, 5, 5 }       // Re-Bump Speed Divisor (Divides the Homing Feedrate)
#define HOMING_BACKOFF_POST_MM { 3, 3, 3 }    // (mm) Backoff from endstops after homing
#define MICROSTEP_MODES { 16, 16, 16, 16, 16, 16 } // [1,2,4,8,16]
#define ADVANCED_PAUSE_FEATURE
  #define ADVANCED_PAUSE_PURGE_FEEDRATE        3  // (mm/s) Extrude feedrate (after loading). Should be slower than load feedrate.
  #define ADVANCED_PAUSE_PURGE_LENGTH         50  // (mm) Length to extrude after loading.
  #define ADVANCED_PAUSE_RESUME_PRIME          0  // (mm) Extra distance to prime nozzle after returning from park.

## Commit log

2022-02-14 Update door stopper.stl
    [door stopper.stl]
2022-02-14 new part
    [LCD cable holder body.stl, LCD cable holder cap.stl]
2022-02-17 modified and add
    [LCD cable holder body.stl, effector cover.stl, mega2560_bracket.stl]
2022-02-19 new files
    [hotend bracket left.stl, hotend bracket right.stl]
2022-02-22 add and modified
    [nozzle set bracket left.stl, nozzle set bracket right.stl]
2022-02-25 Update Delta Square V1 BOM.pdf
2022-03-04 Update spool core.stl
    [spool core.stl]
2022-08-01 added and modified
    [Leveling_fixed bar.stl, Leveling_sensor.stl, X-idle belt supporter.stl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]
2022-10-15 Update cooler parts.stl
    [cooler parts.stl]
2023-02-26 Update effector Direct cover.stl
    [effector Direct cover.stl]
2023-02-26 Create Delta arm shoe.stl
    [Delta arm shoe.stl]
2023-07-24 Update DS-pro assembly manual_02.pdf

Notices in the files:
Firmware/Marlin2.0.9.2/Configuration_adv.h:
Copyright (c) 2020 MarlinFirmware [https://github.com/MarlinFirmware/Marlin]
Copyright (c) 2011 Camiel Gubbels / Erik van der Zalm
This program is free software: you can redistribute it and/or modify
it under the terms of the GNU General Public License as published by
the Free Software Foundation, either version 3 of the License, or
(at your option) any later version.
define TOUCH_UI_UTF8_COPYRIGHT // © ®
